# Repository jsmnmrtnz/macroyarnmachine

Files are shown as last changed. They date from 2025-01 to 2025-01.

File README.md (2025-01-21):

Hey!
How exciting you want to build the Macro Yarn Machine. I have built this machine as part of my Master’s project in 2024, and I would have never been able to build it without relying on published Open-Source Hardware projects and the community.

Therefor I want to credit:

1.) Circular Knitic by Varvara Guljajeva and Canet Sola, 2014. https://github.com/var-mar/circular_knitic

2.) HILO Spinning Machine. As I have been working with Sara Diaz Rodriguez closely for the past 2 years and learned about Open-Source Hardware for Textiles from her. https://www.hilotextiles.com/

If you want to credit my machine, please use:
„Macro Yarn Machine“ by Jasmin Martinez, 2024

further information:
Master Thesis: Martinez, Jasmin. Hacking Textile Tools. 2024. Kunsthochschule Weißensee (Weissensee Art Academy).
Mentored by Prof. Christiane Sauer and Prof. Dr. Lucy Norris.

Note: I reverse-documented building the machine, which should explain why the parts are full of soil and grease. Please excuse this and let me know if it makes anything unclear to you. Now – let’s start building!

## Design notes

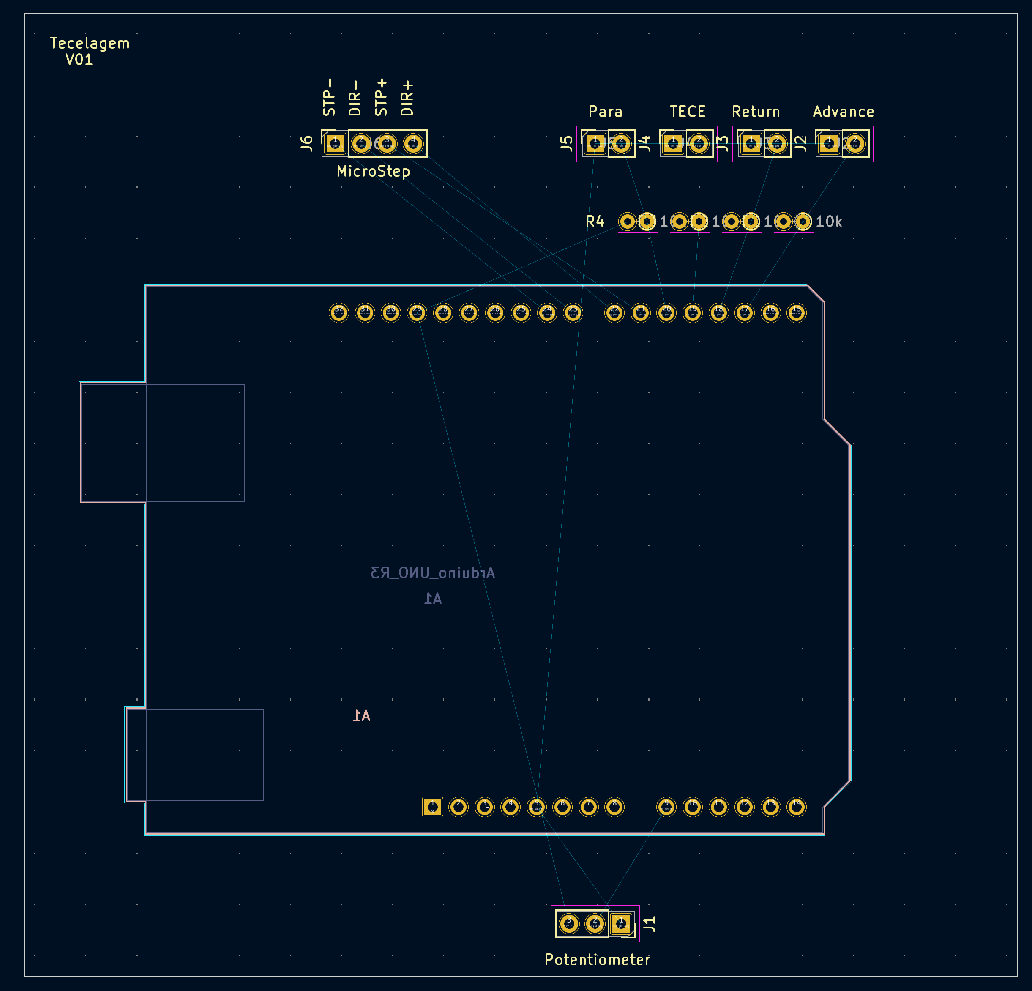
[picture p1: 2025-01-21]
3_Arduino-Electronics/Bildschirmfoto 2024-07-24 um 17.11.13.png

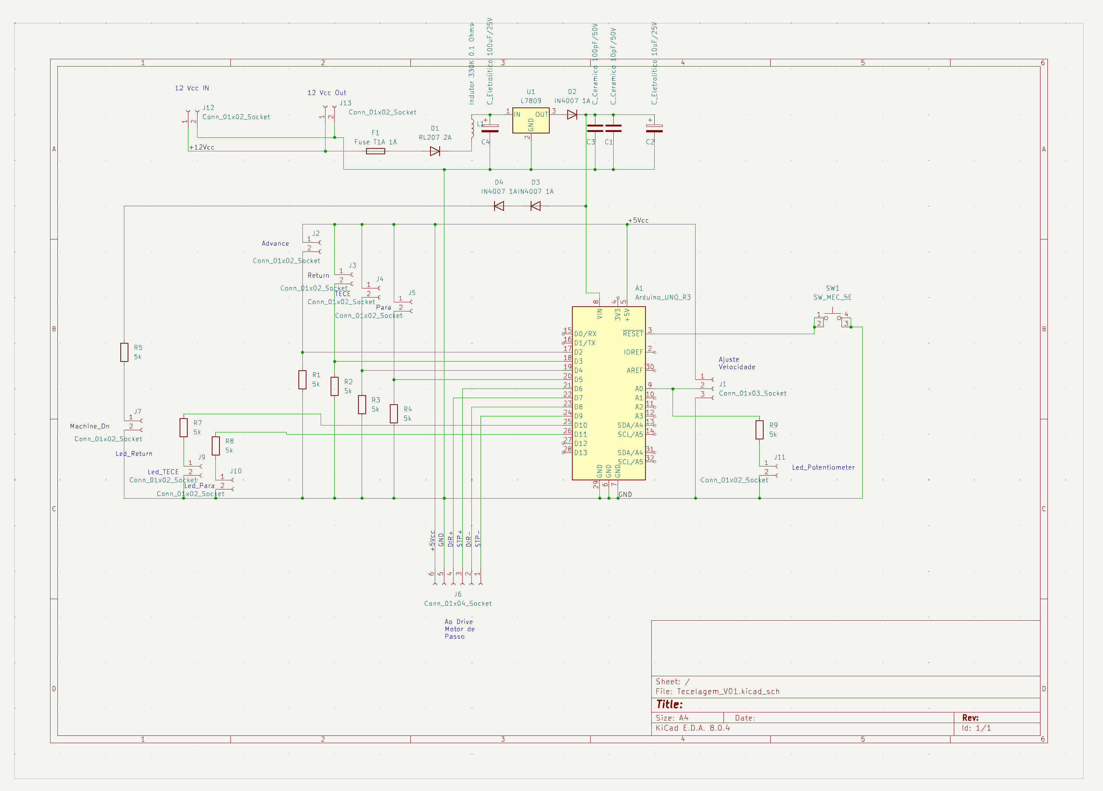
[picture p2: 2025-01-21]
3_Arduino-Electronics/Bildschirmfoto 2024-07-24 um 17.09.53.png

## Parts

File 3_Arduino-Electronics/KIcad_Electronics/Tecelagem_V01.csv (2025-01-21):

# | Reference | Qty | Value | Footprint | DNP
1 | A1 | 1 | Arduino_UNO_R3 | Module:Arduino_UNO_R3
2 | C1 | 1 | C_Ceramico 10pF/50V | Capacitor_THT:C_Disc_D3.0mm_W1.6mm_P2.50mm
3 | C2 | 1 | C_Eletrolitico 10uF/25V | Capacitor_THT:CP_Radial_D5.0mm_P2.50mm
4 | C3 | 1 | C_Ceramico 100pF/50V | Capacitor_THT:C_Disc_D3.0mm_W1.6mm_P2.50mm
5 | C4 | 1 | C_Eletrolitico 100uF/25V | Capacitor_THT:CP_Radial_D5.0mm_P2.50mm
6 | D1 | 1 | RL207 2A | Diode_THT:D_DO-27_P5.08mm_Vertical_AnodeUp
7 | D2, D3, D4 | 3 | IN4007 1A | Diode_THT:D_DO-15_P3.81mm_Vertical_AnodeUp
8 | F1 | 1 | Fuse T1A 1A | Fuse:Fuse_Littelfuse_372_D8.50mm
9 | J1 | 1 | Conn_01x03_Socket | Connector_Molex:Molex_KK-254_AE-6410-03A_1x03_P2.54mm_Vertical
10 | J2, J3, J4, J5, J7, J9, J10, J11 | 8 | Conn_01x02_Socket | Connector_Molex:Molex_KK-254_AE-6410-02A_1x02_P2.54mm_Vertical
11 | J6 | 1 | Conn_01x04_Socket | Connector_Molex:Molex_KK-254_AE-6410-06A_1x06_P2.54mm_Vertical
12 | J12, J13 | 2 | Conn_01x02_Socket | Connector_Molex:Molex_KK-396_A-41791-0002_1x02_P3.96mm_Vertical
13 | L1 | 1 | Indutor 330K 0,1 Ohms | Inductor_THT:L_Radial_D7.8mm_P5.00mm_Fastron_07HCP
14 | R1, R2, R3, R4, R5, R7, R8, R9 | 8 | 5k | Resistor_THT:R_Axial_DIN0204_L3.6mm_D1.6mm_P1.90mm_Vertical
15 | SW1 | 1 | SW_MEC_5E | Chave_Tactil:Tactil_6mm
16 | U1 | 1 | L7809 | Package_TO_SOT_THT:TO-126-3_Vertical

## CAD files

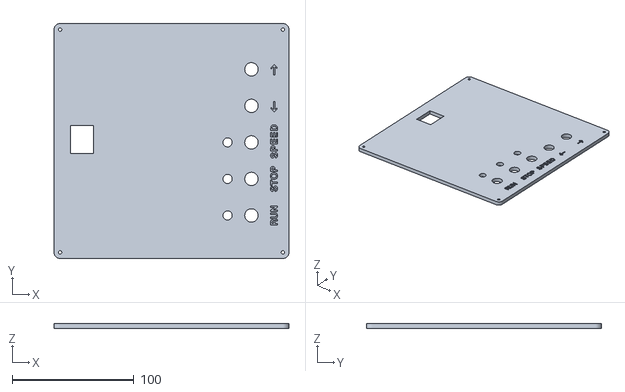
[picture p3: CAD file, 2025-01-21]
2_STLs/Electronic Board/Electronics-Control-Board.stl
193.0 x 193.0 x 4.00

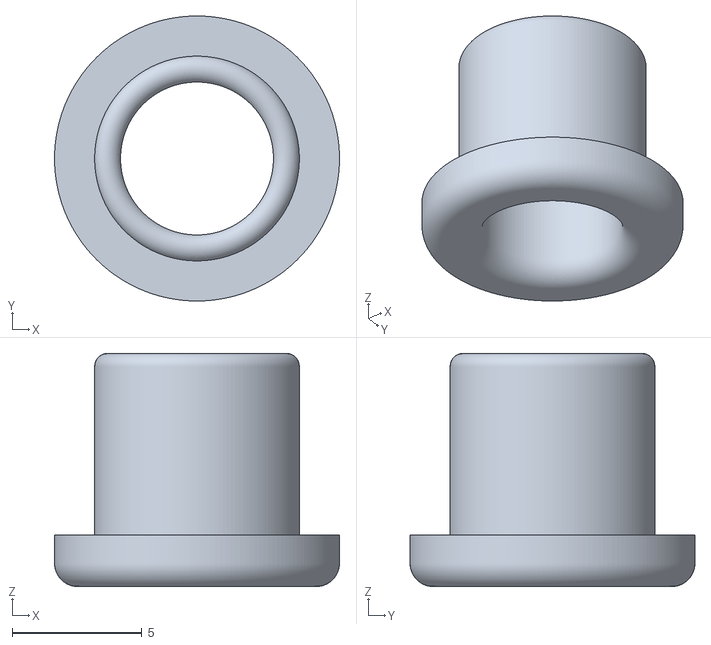
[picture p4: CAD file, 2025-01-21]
2_STLs/Eyelet.stl
11.0 x 11.0 x 9.00

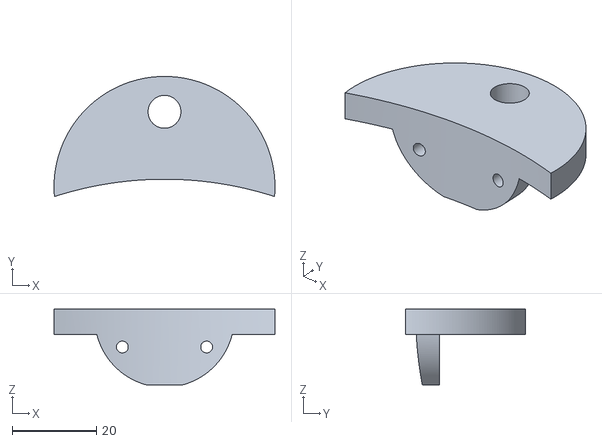
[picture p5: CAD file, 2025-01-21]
2_STLs/Machine Body/4xHolder-for-threaded-rods.stl
52.4 x 28.5 x 18.0

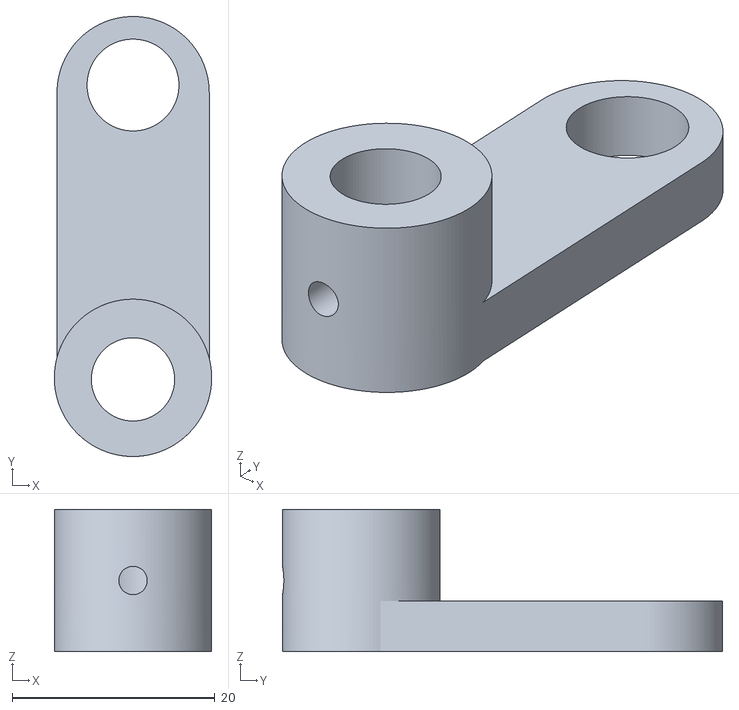
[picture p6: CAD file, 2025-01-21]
2_STLs/Yarn Guidance/4x-yarn-wing-guide.stl
15.5 x 43.3 x 14.0

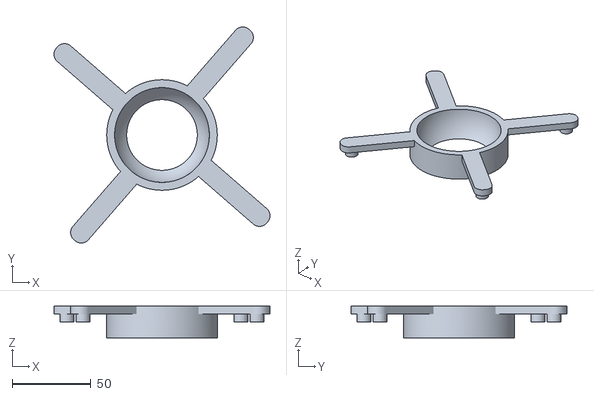
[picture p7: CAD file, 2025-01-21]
2_STLs/funnel.stl
136.8 x 136.8 x 20.0

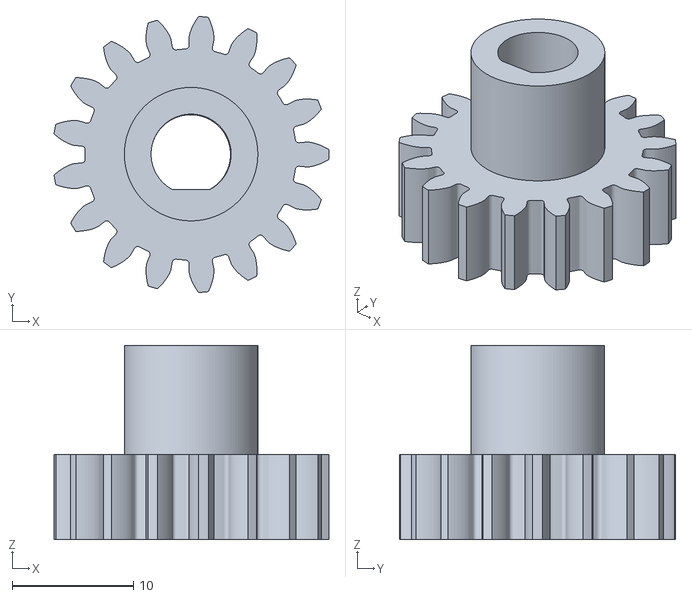
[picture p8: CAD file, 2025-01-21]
2_STLs/Machine Body/small-motor-gear2.stl
22.7 x 22.8 x 16.0

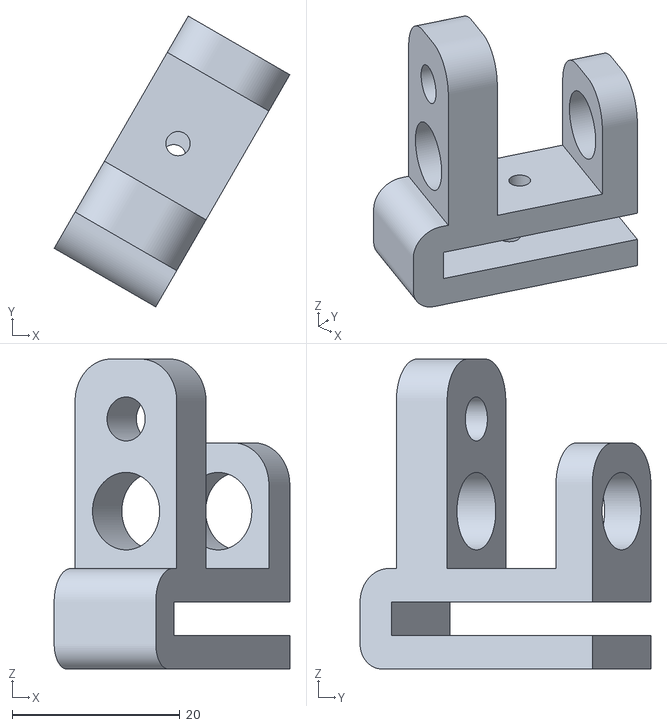
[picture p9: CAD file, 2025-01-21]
2_STLs/Yarn Guidance/4x-yarn-tension-holder.stl
28.1 x 34.7 x 37.0

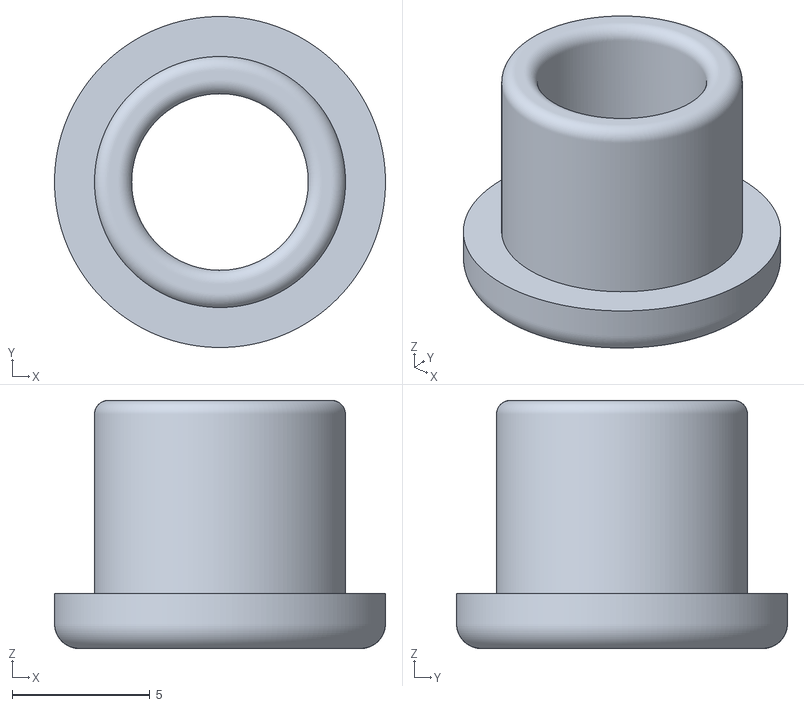
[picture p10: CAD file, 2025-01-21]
2_STLs/eyelet-final.stl
12.0 x 12.0 x 9.00

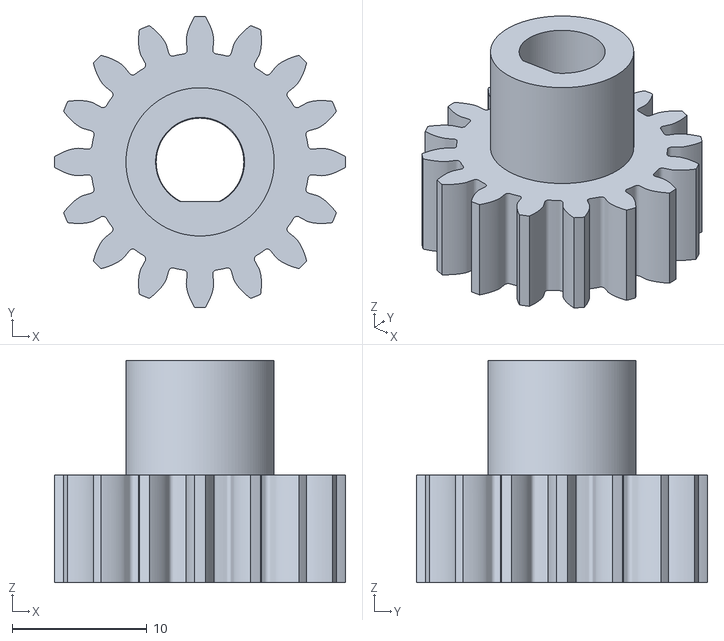
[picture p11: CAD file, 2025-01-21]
2_STLs/Machine Body/small-motor-gear-1.stl
21.6 x 21.6 x 16.5

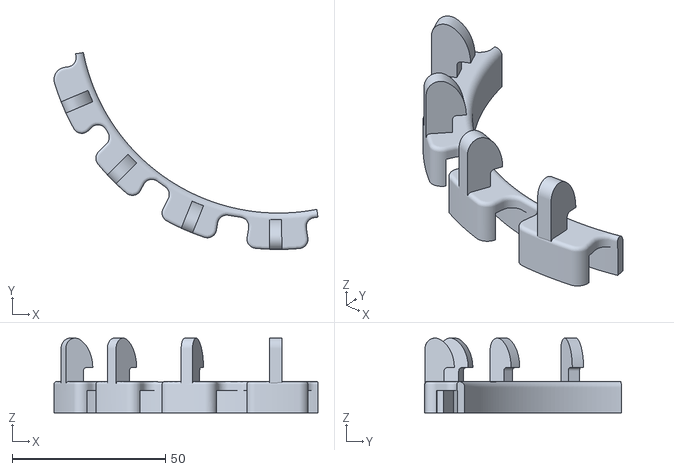
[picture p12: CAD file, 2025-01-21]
2_STLs/Yarn Guidance/Needle-Holder.stl
86.1 x 64.2 x 24.4

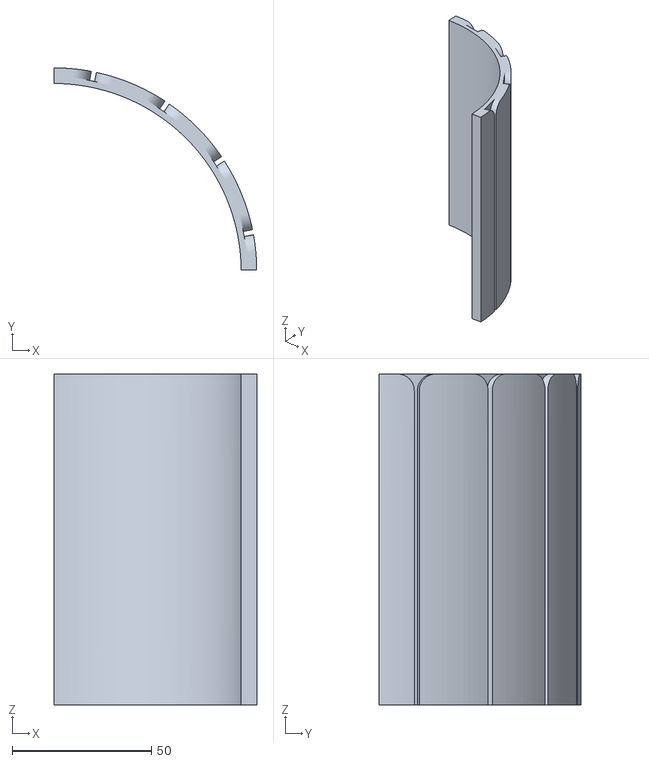
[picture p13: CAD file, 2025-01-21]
2_STLs/Machine Body/4x-inner-cylinder.stl
72.8 x 72.7 x 119.0

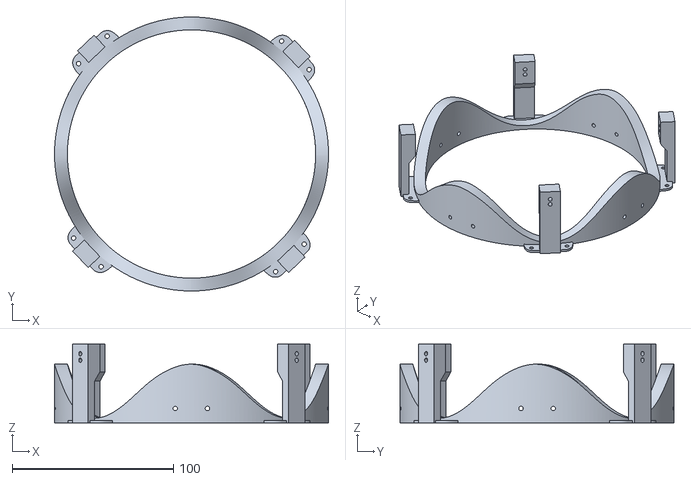
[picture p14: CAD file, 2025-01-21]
2_STLs/Machine Body/needle-guide-bottom.stl
170.0 x 170.0 x 49.0

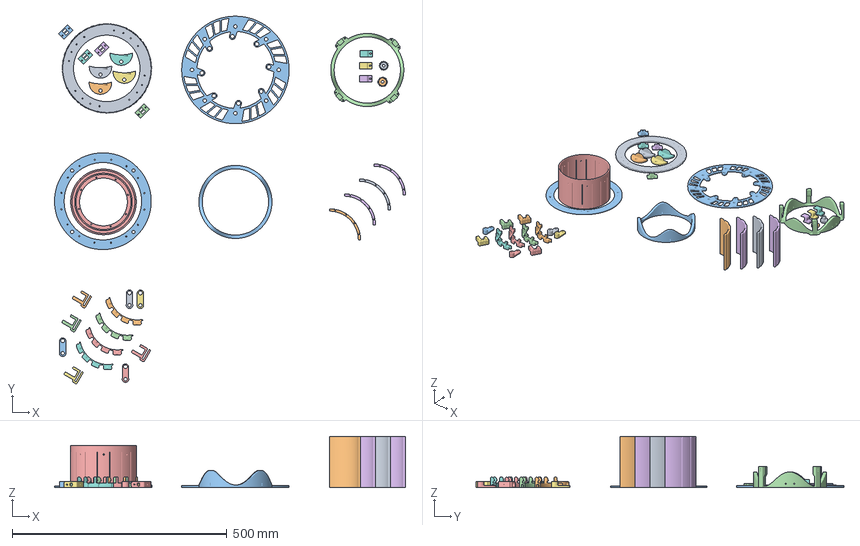
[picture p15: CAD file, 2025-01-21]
2_STLs/Machine Body/4xBearings.3mf
816.6 x 855.3 x 119.0 mm
Big Bottom Gear.stl
Needle-Holder.stl x 4
needle-guide-top.stl
4x-inner-cylinder.stl x 4
4xHolder-for-threaded-rods.stl x 4
4x-yarn-tension-holder.stl x 4
4xBearings.stl x 4
4x-yarn-wing-guide.stl x 4
Middle-Layer.stl
needle-guide-bottom.stl
Outer-Cylinder-Final.stl
Bottom-Gear-Fix.stl x 3
small-motor-gear-1.stl
small-motor-gear2.stl
Top-Layer.stl

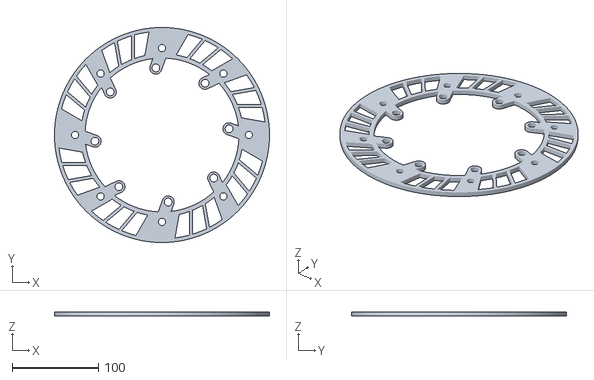
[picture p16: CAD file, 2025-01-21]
2_STLs/Machine Body/Middle-Layer.stl
250.0 x 250.0 x 5.00

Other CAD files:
2_STLs/Machine Body/needle-guide-top.stl
2_STLs/Machine Body/Bottom-Gear-Fix.stl
2_STLs/Machine Body/Outer-Cylinder-Final.stl
2_STLs/Machine Body/Top-Layer.stl
2_STLs/Machine Body/4xBearings.stl
2_STLs/Machine Body/Big Bottom Gear.stl

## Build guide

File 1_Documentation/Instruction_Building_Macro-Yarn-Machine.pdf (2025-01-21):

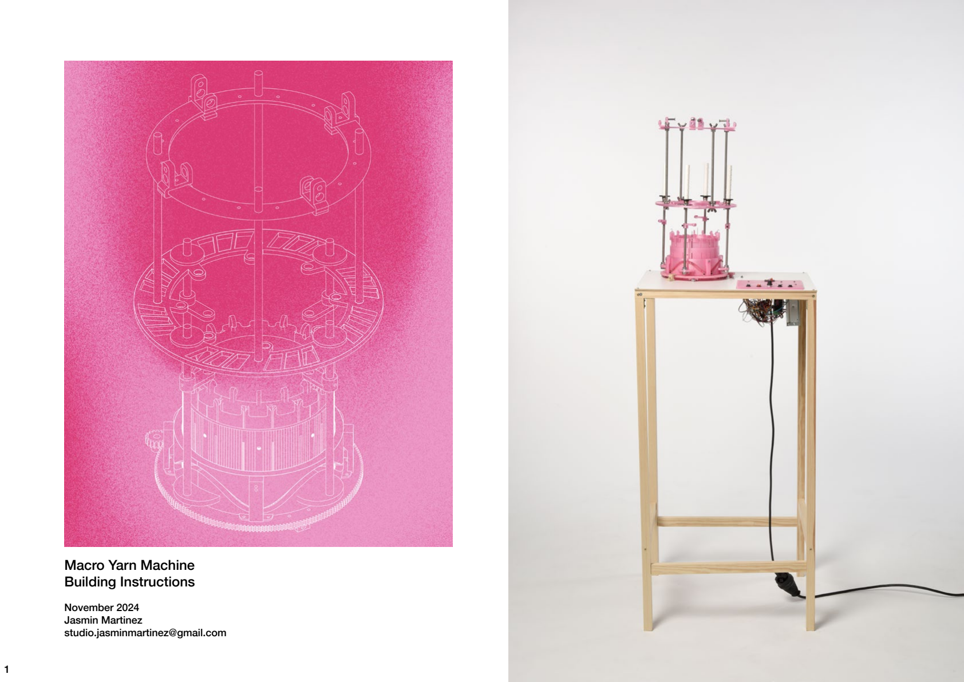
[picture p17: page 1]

Macro Yarn Machine
Building Instructions

November 2024
Jasmin Martinez
studio.jasminmartinez@gmail.com

Hey!
How exciting you want to build the Macro Yarn Machine. I have built this machine as part of my Master’s project in 2024, and I would have never been able to build it without relying on published Open-Source Hardware projects and the community.
Therefor I want to credit:
1.) Circular Knitic by Varvara Guljajeva and Canet Sola, 2014. https://github.com/var-mar/circular_knitic
2.) HILO Spinning Machine. As I have been working with Sara Diaz Rodriguez closely for the past 2 years and learned about Open Textile Hardware from her. https://www.hilotextiles.com/
If you want to credit my machine, please use:
„Macro Yarn Machine“ by Jasmin Martinez, 2024
further information:
Master Thesis: Martinez, Jasmin. Hacking Textile Tools. 2024. Kunsthochschule Weißensee (Weissensee Art Academy). Mentored by Prof. Christiane Sauer and Prof. Dr. Lucy Norris. Note: I reverse-documented building the machine, which should explain why the parts are full of soil and grease. Please excuse this and let me know if it makes anything un-clear to you.
Now – let’s start building!

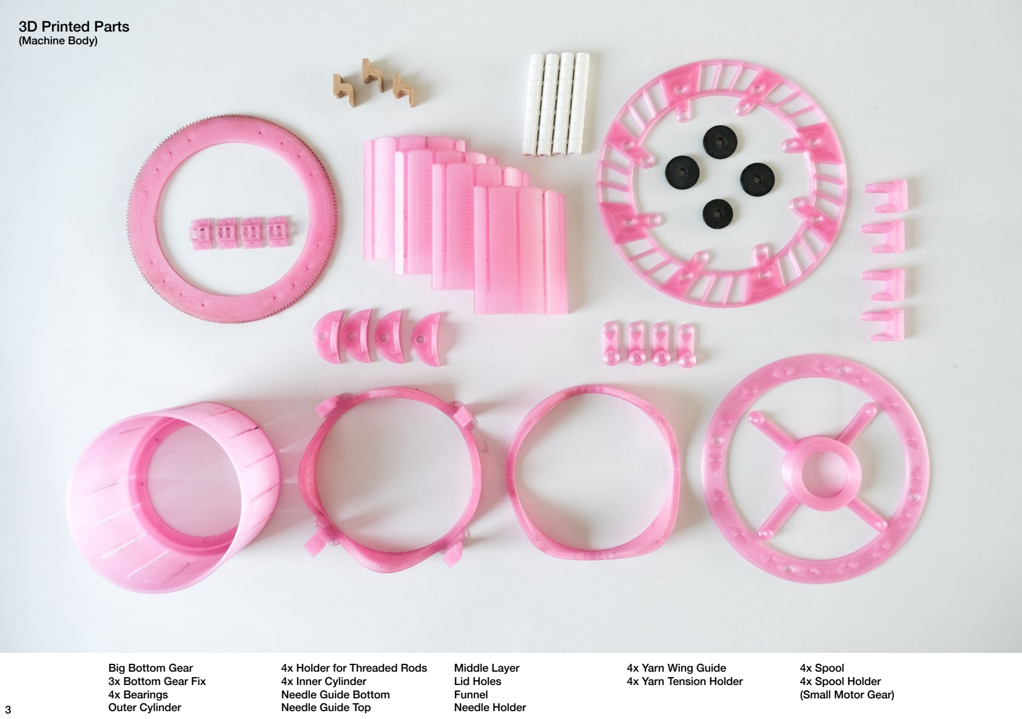
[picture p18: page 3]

3D Printed Parts
(Machine Body)

Big Bottom Gear
3x Bottom Gear Fix
4x Bearings
Outer Cylinder

4x Holder for Threaded Rods 4x Inner Cylinder
Needle Guide Bottom
Needle Guide Top

Middle Layer
Lid Holes
Funnel
Needle Holder

4x Yarn Wing Guide
4x Yarn Tension Holder

4x Spool
4x Spool Holder
(Small Motor Gear)

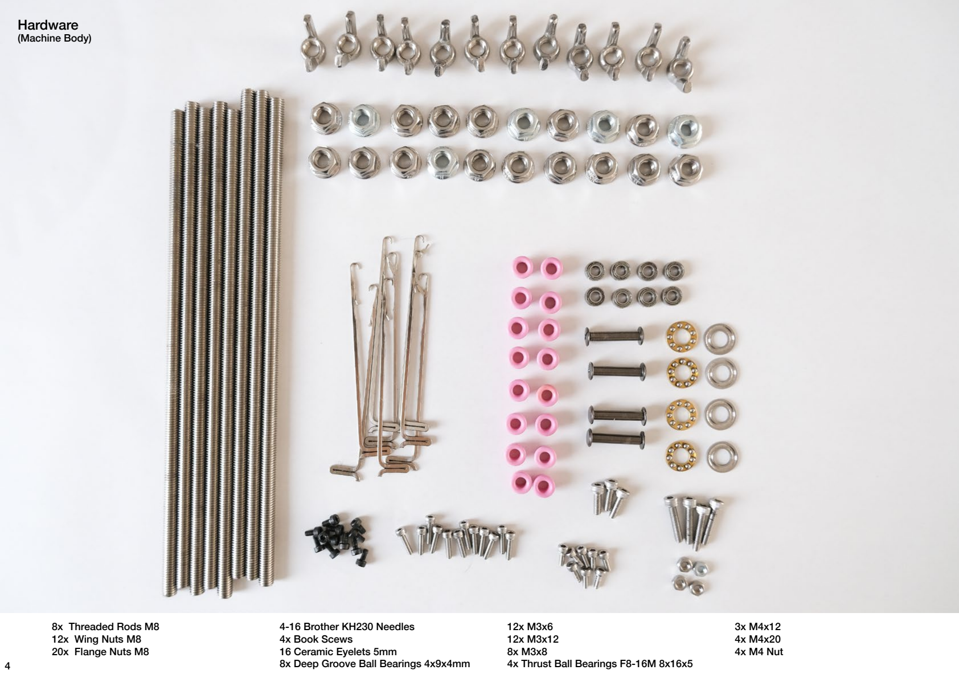
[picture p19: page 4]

Hardware
(Machine Body)

8x Threaded Rods M8
12x Wing Nuts M8
20x Flange Nuts M8

4-16 Brother KH230 Needles
4x Book Scews
16 Ceramic Eyelets 5mm
8x Deep Groove Ball Bearings 4x9x4mm

12x M3x6
12x M3x12
8x M3x8
4x Thrust Ball Bearings F8-16M 8x16x5

3x M4x12
4x M4x20
4x M4 Nut

Bottom Gear

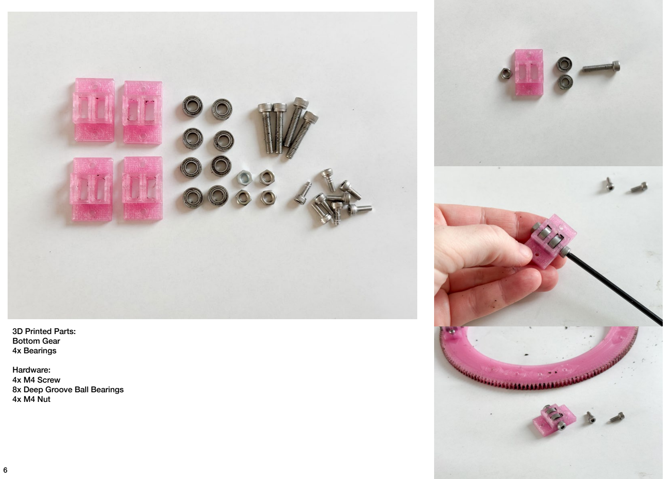
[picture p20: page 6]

3D Printed Parts:
Bottom Gear
4x Bearings
Hardware:
4x M4 Screw
8x Deep Groove Ball Bearings 4x M4 Nut

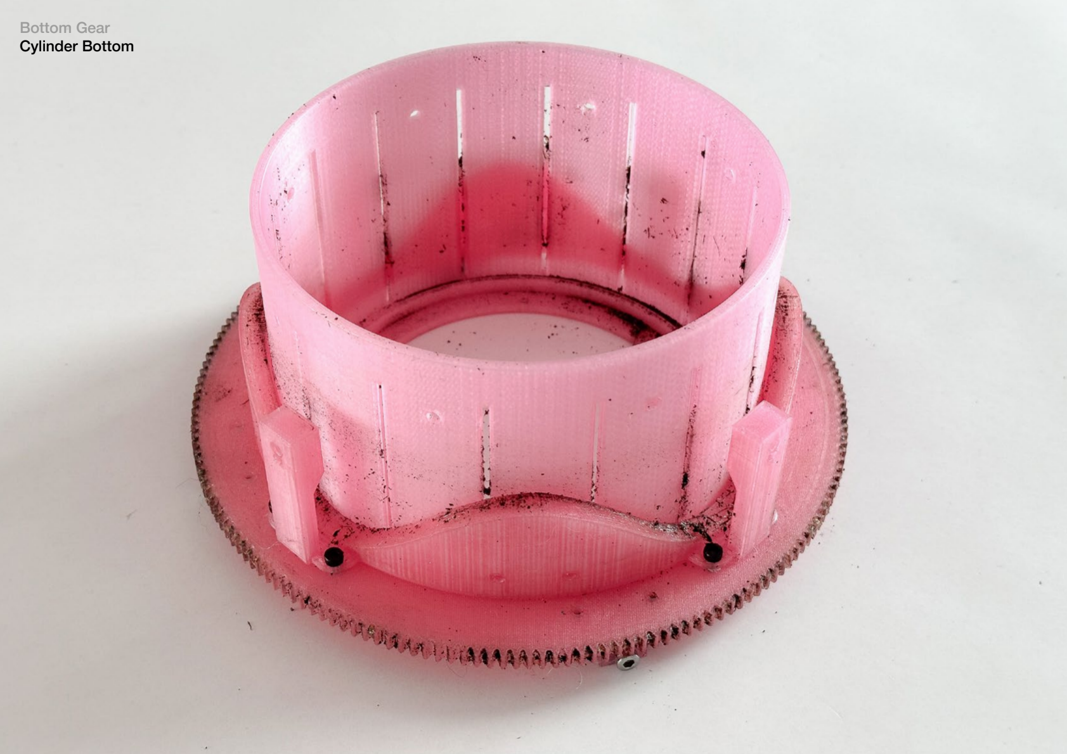
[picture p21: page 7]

Bottom Gear
Cylinder Bottom

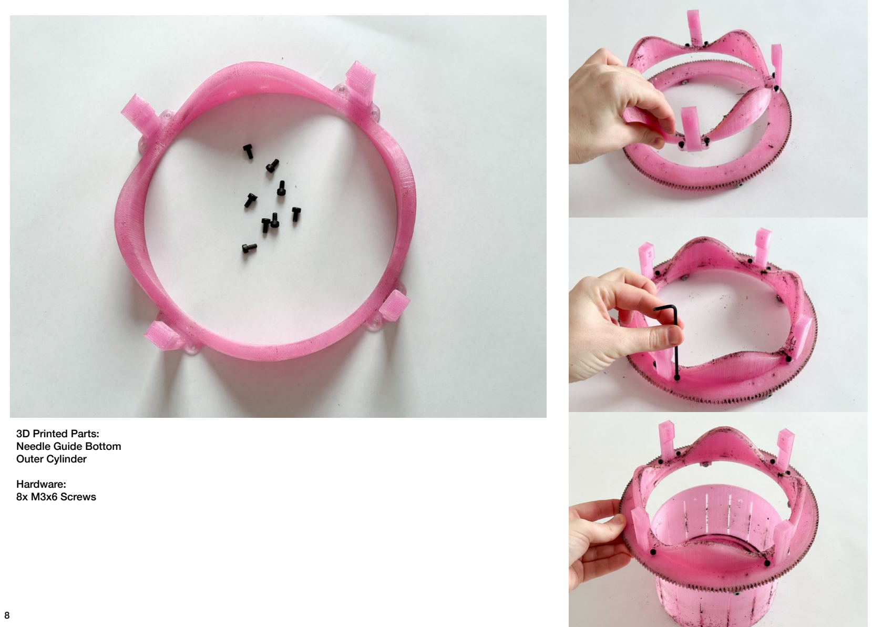
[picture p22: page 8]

3D Printed Parts:
Needle Guide Bottom
Outer Cylinder
Hardware:
8x M3x6 Screws

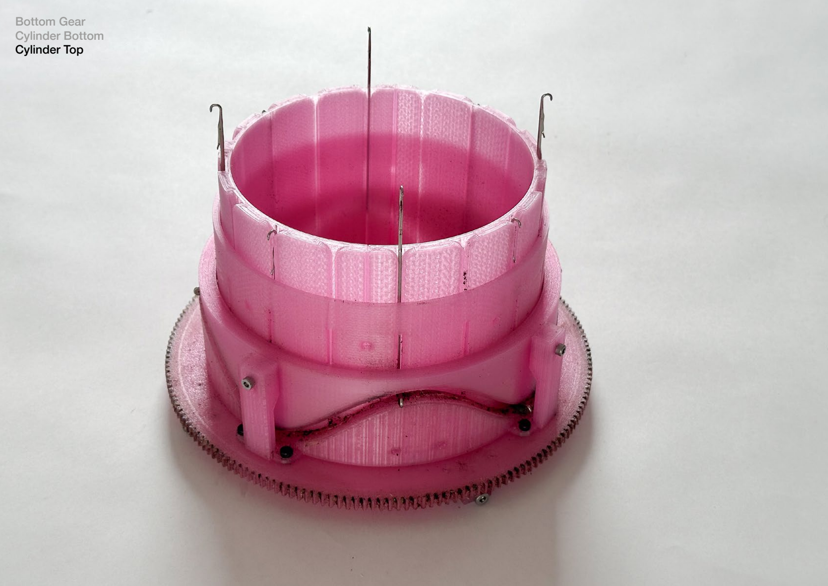
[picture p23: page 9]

Bottom Gear
Cylinder Bottom
Cylinder Top

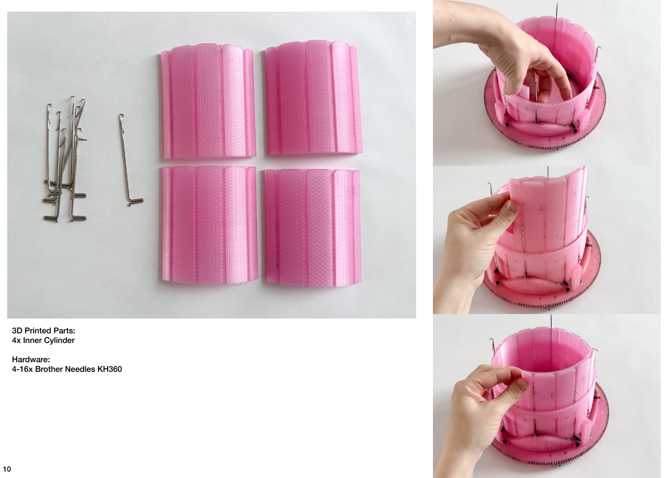
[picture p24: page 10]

3D Printed Parts:
4x Inner Cylinder
Hardware:
4-16x Brother Needles KH360

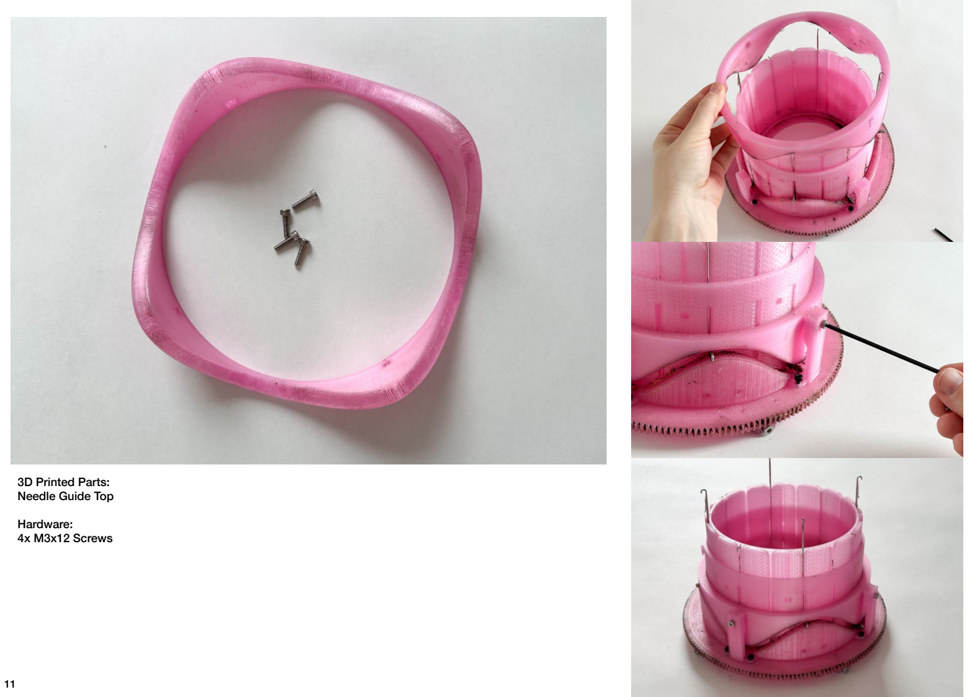
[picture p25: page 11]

3D Printed Parts:
Needle Guide Top
Hardware:
4x M3x12 Screws

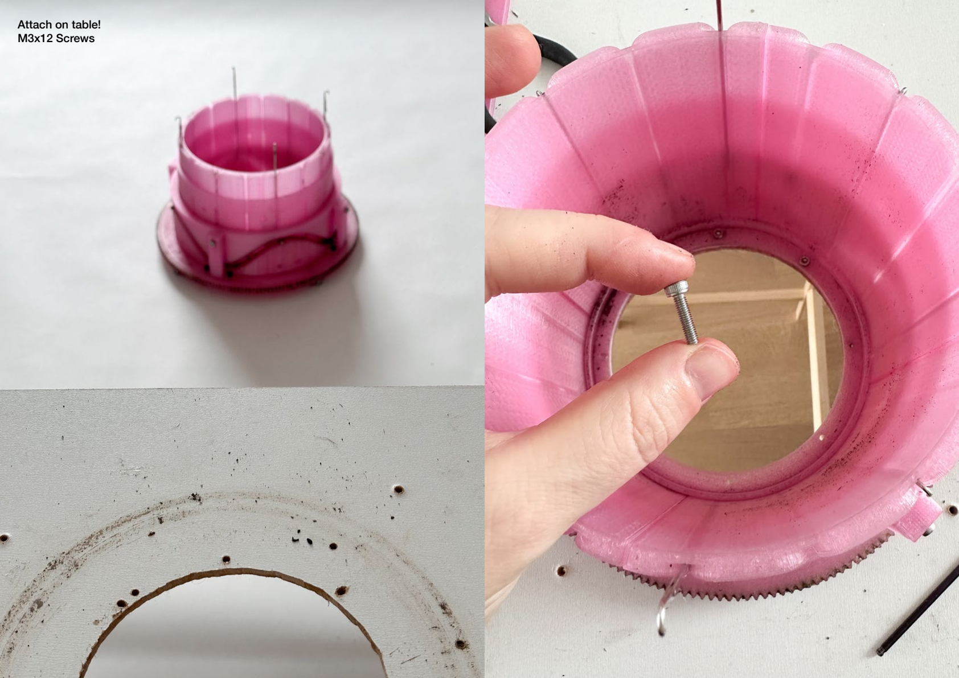
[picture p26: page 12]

Attach on table!
M3x12 Screws

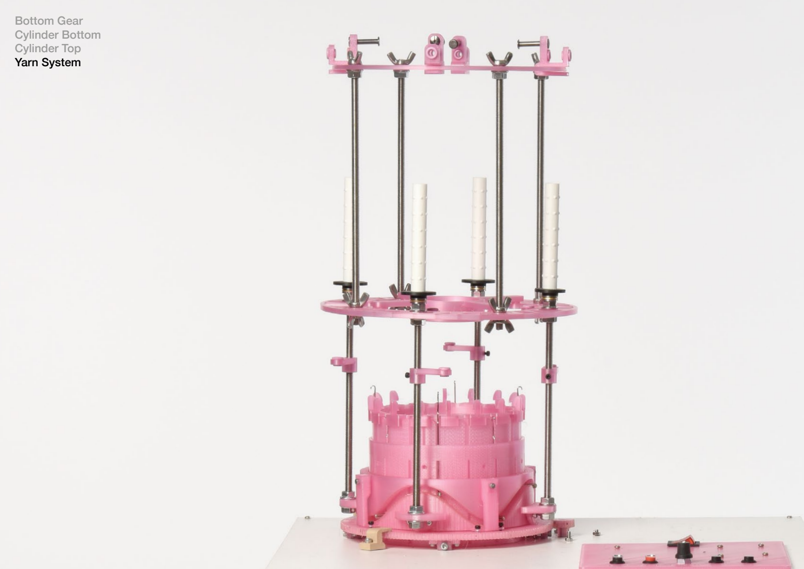
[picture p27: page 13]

Bottom Gear
Cylinder Bottom
Cylinder Top
Yarn System

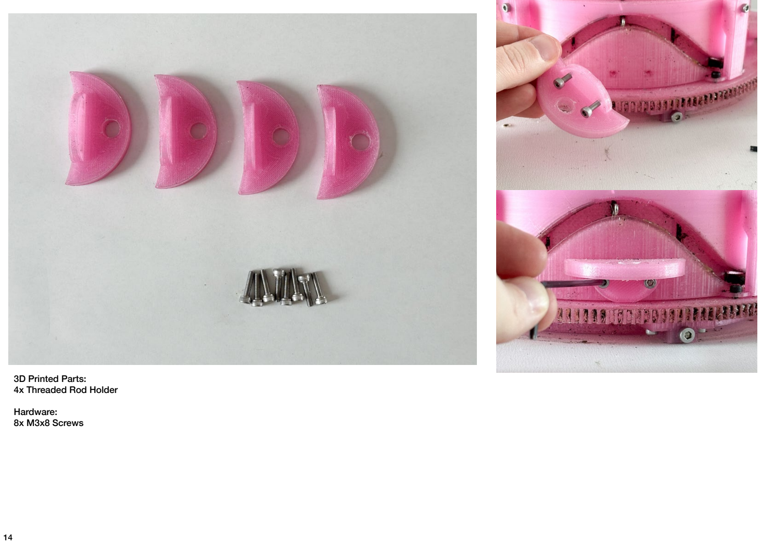
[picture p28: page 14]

3D Printed Parts:
4x Threaded Rod Holder
Hardware:
8x M3x8 Screws

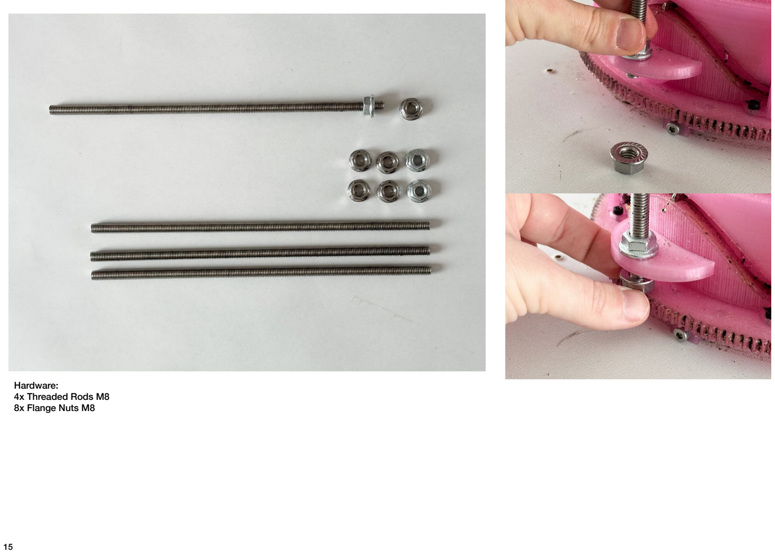
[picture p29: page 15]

Hardware:
4x Threaded Rods M8
8x Flange Nuts M8

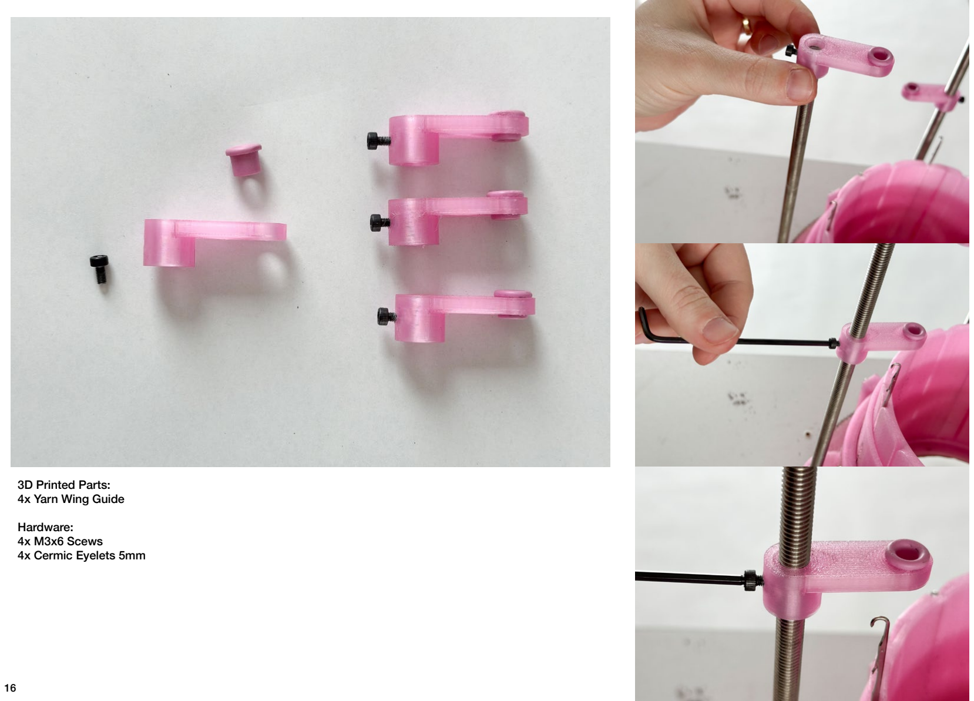
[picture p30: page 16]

3D Printed Parts:
4x Yarn Wing Guide
Hardware:
4x M3x6 Scews
4x Cermic Eyelets 5mm

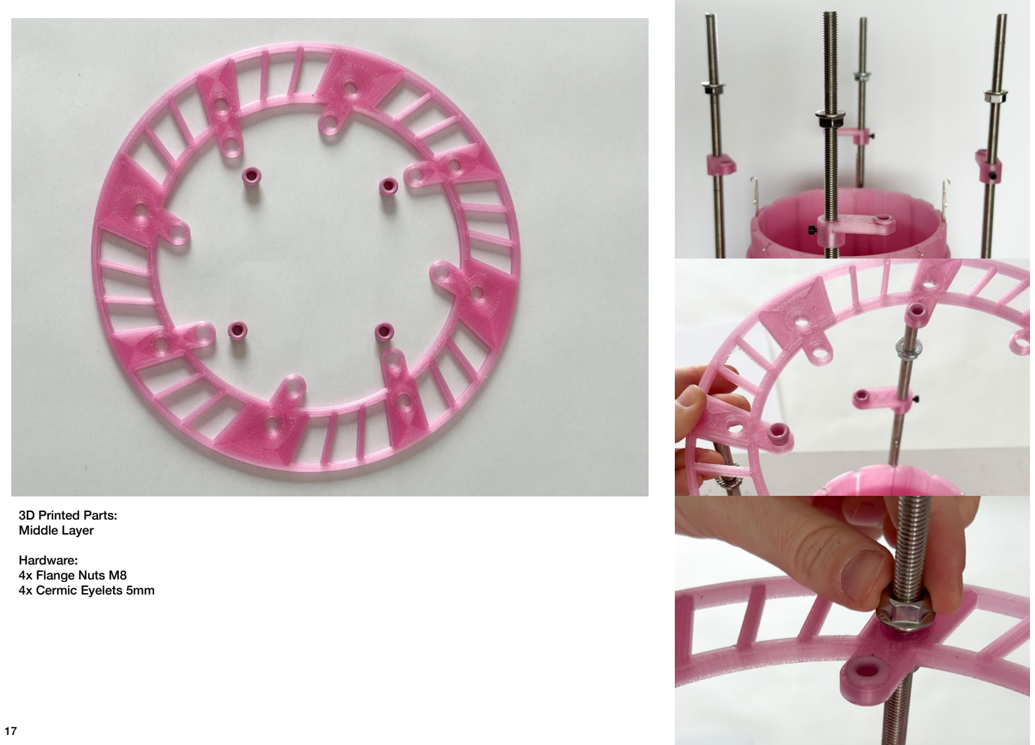
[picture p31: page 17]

3D Printed Parts:
Middle Layer
Hardware:
4x Flange Nuts M8
4x Cermic Eyelets 5mm

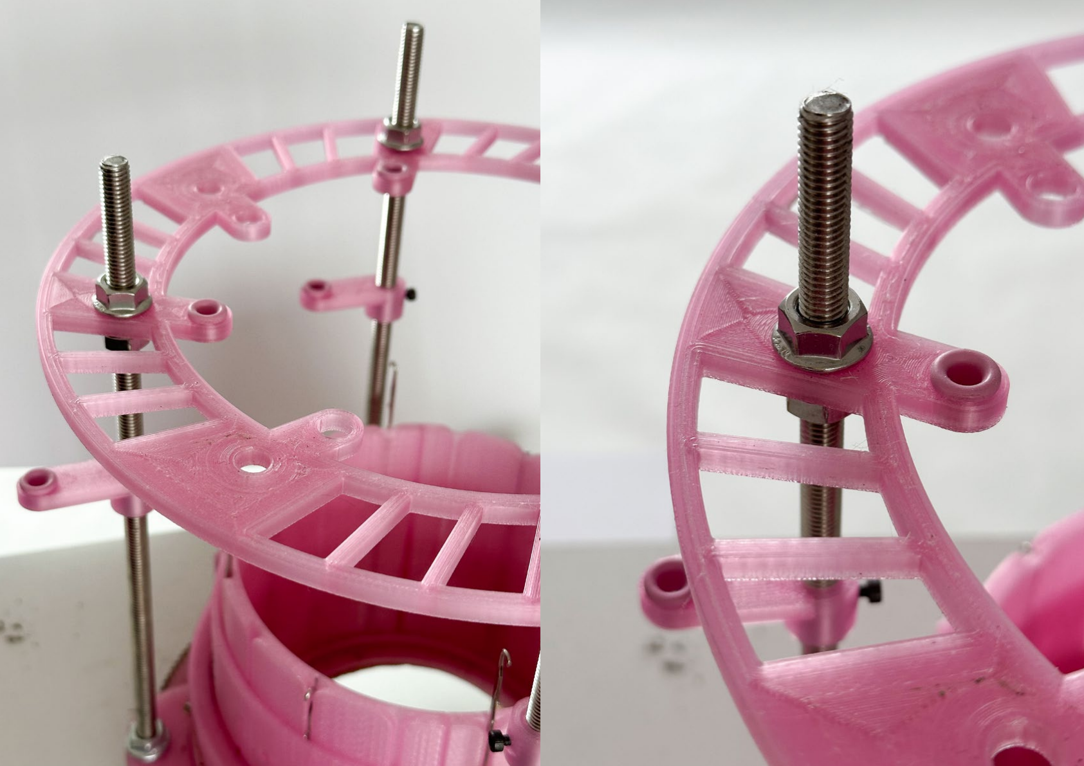
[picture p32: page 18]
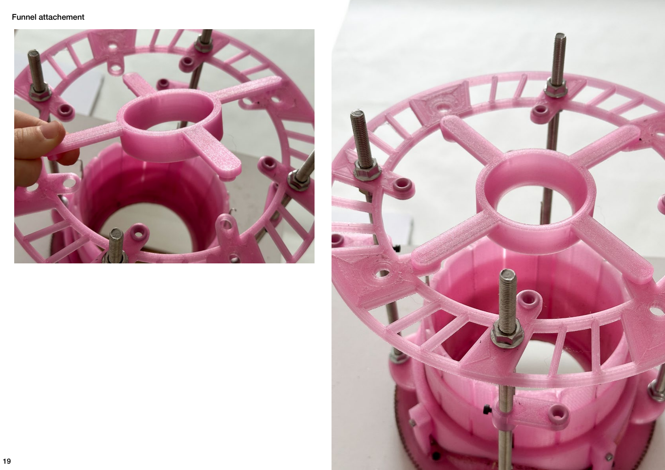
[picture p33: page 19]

Funnel attachement

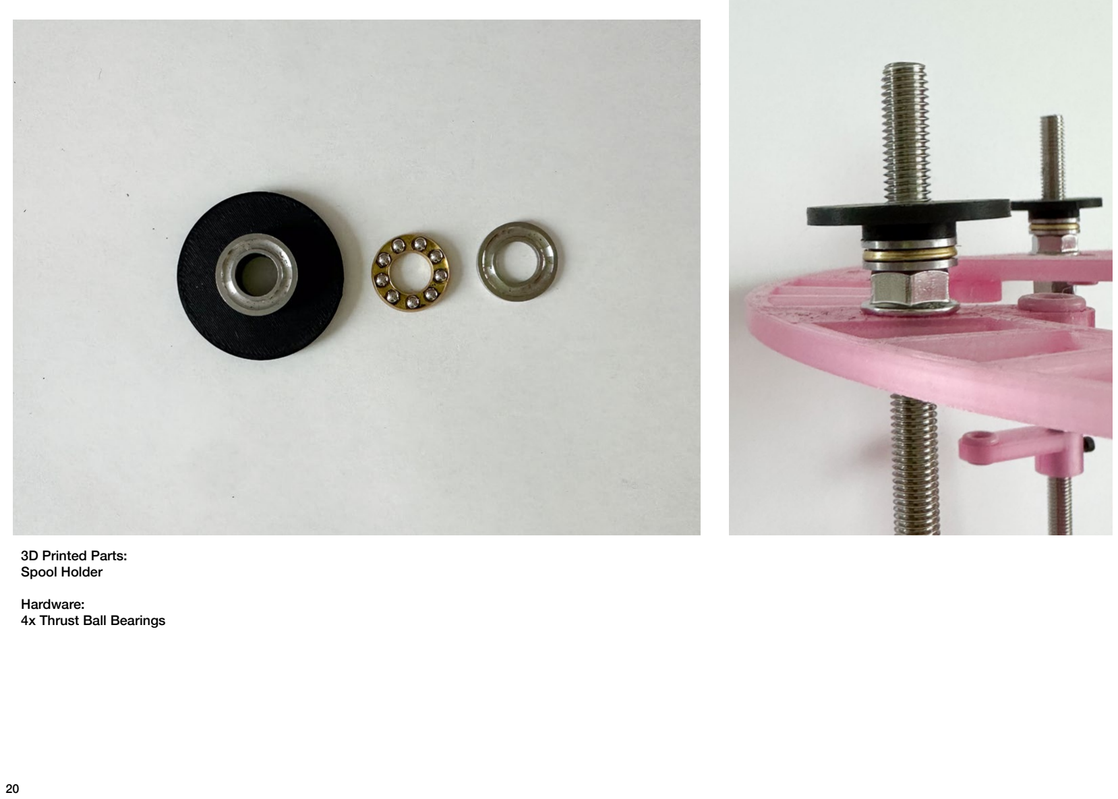
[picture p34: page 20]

3D Printed Parts:
Spool Holder
Hardware:
4x Thrust Ball Bearings

Hardware:
8x Wing Nuts M8
4x Threaded Rods M8

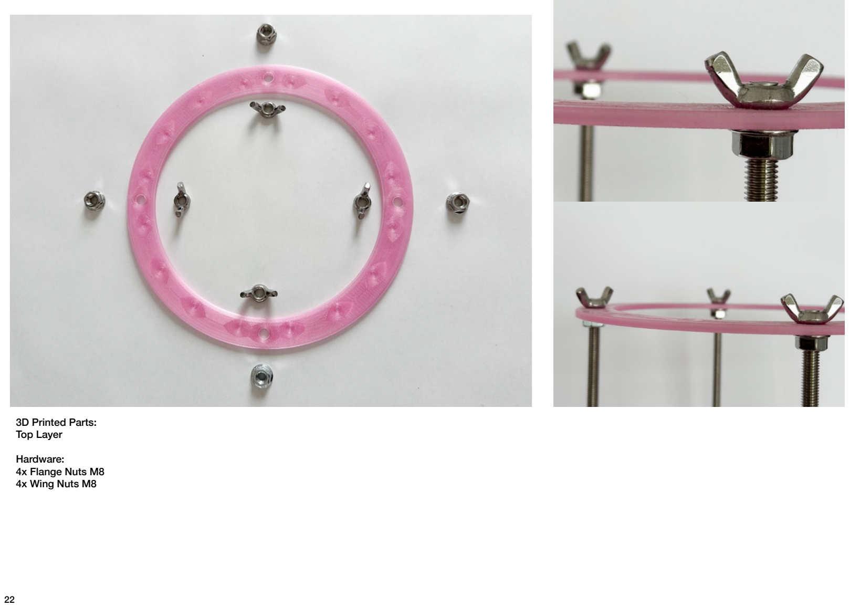
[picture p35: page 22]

3D Printed Parts:
Top Layer
Hardware:
4x Flange Nuts M8
4x Wing Nuts M8

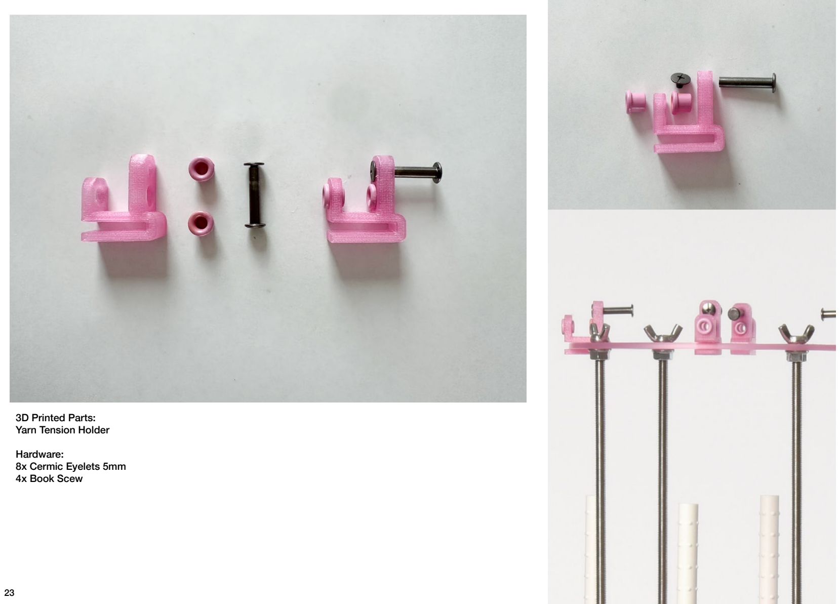
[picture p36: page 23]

3D Printed Parts:
Yarn Tension Holder
Hardware:
8x Cermic Eyelets 5mm
4x Book Scew

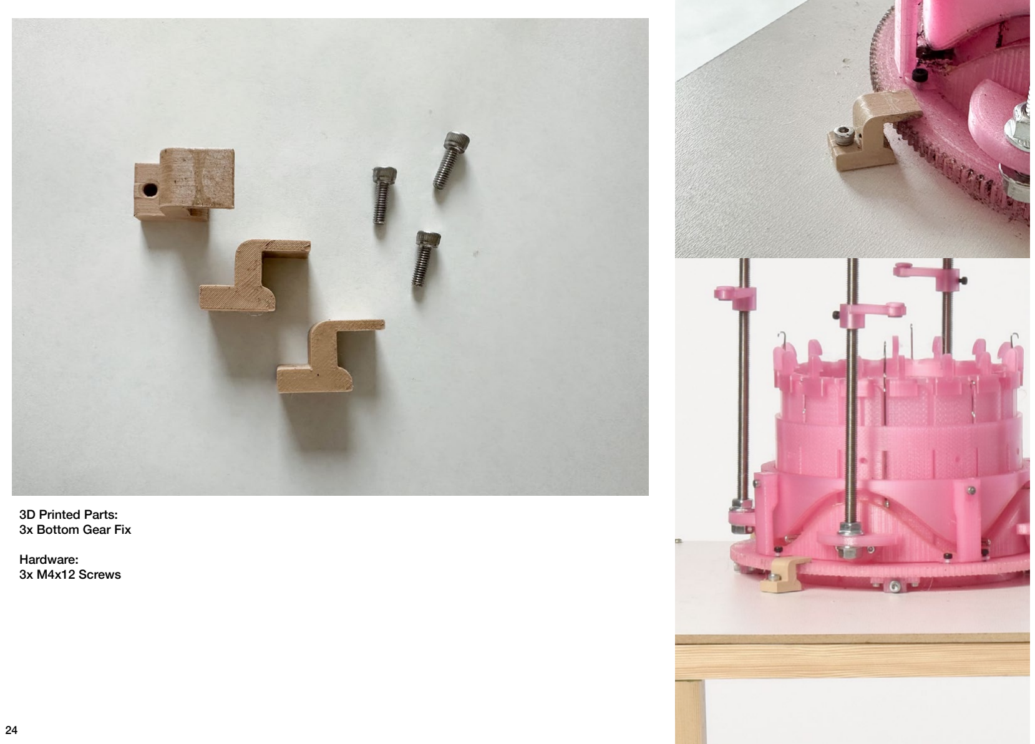
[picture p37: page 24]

3D Printed Parts:
3x Bottom Gear Fix
Hardware:
3x M4x12 Screws

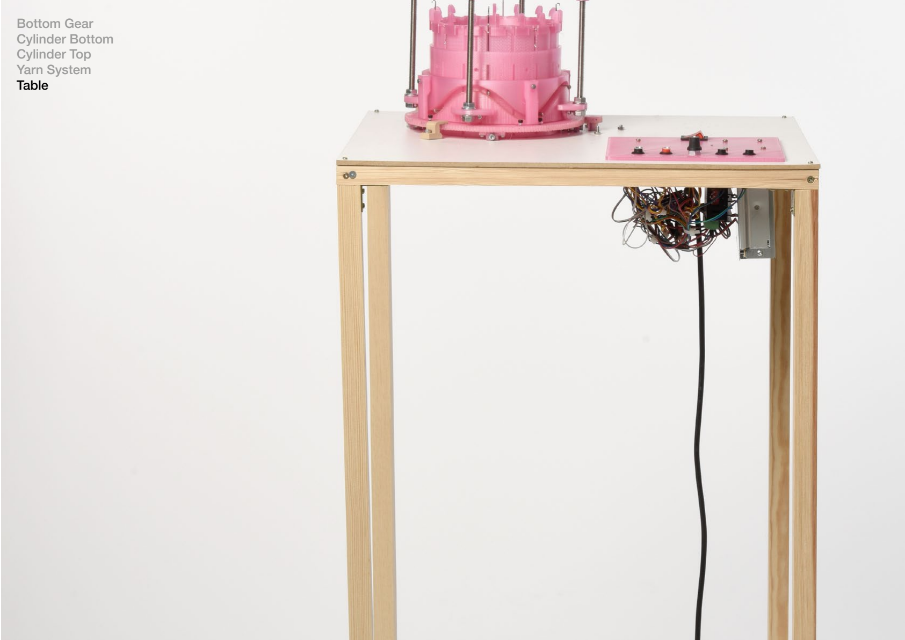
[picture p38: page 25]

Bottom Gear
Cylinder Bottom
Cylinder Top
Yarn System
Table

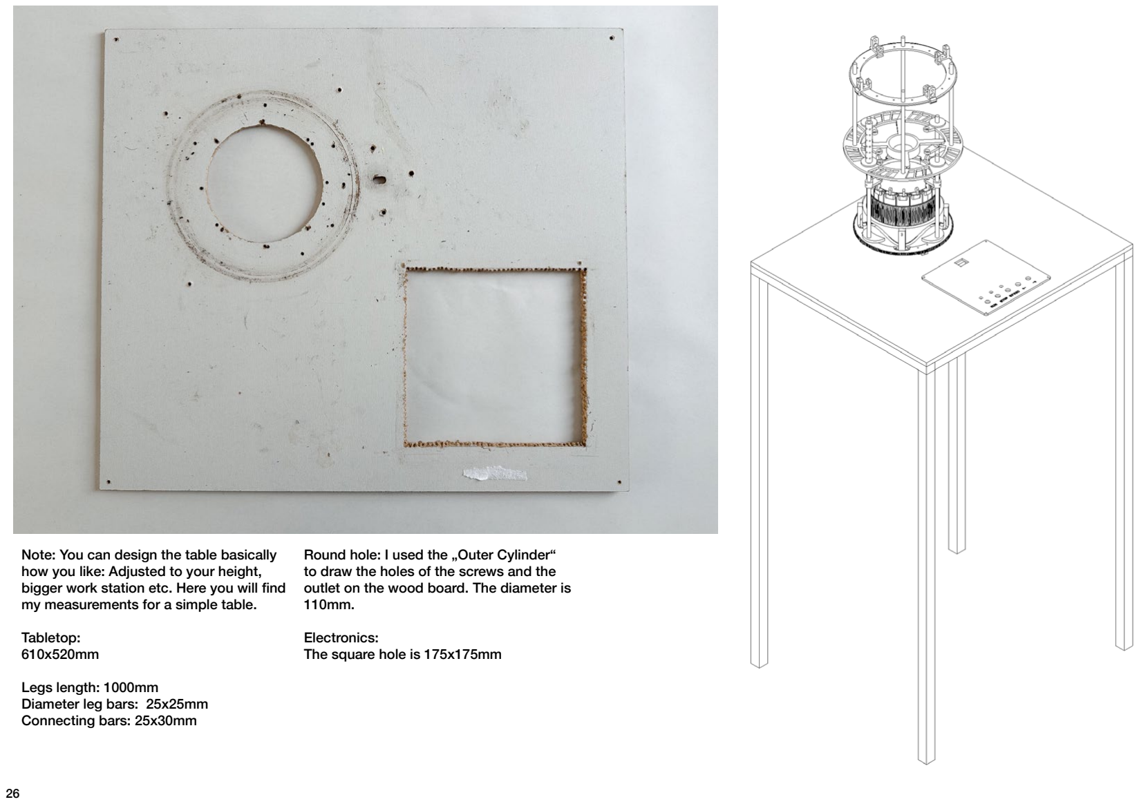
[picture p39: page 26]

Note: You can design the table basically how you like: Adjusted to your height, bigger work station etc. Here you will find my measurements for a simple table. Tabletop:
610x520mm
Legs length: 1000mm
Diameter leg bars: 25x25mm Connecting bars: 25x30mm

Round hole: I used the „Outer Cylinder“ to draw the holes of the screws and the outlet on the wood board. The diameter is 110mm.
Electronics:
The square hole is 175x175mm

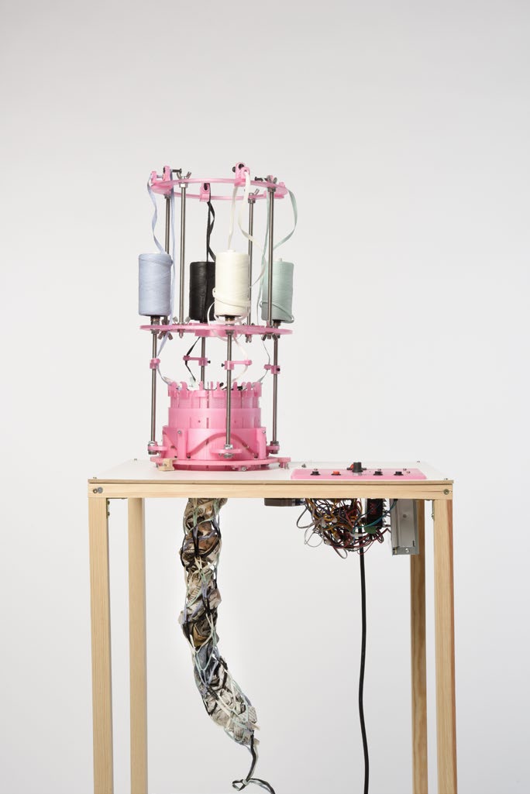
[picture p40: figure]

End Notes:
You will find a STL File named „Needle Holder“ – you can also print those but I had the feeling it doesn’t quite work the way it should. Any feedback is welcome!
Anyway: You build your Macro Yarn Machine
– congratulations!
I’m happy to collaborate for further developments, contact me via E-Mail: studio.jasminmartinez@gmail.com
Let me and others find your process and developments via the hashtag #macroyarnmachine

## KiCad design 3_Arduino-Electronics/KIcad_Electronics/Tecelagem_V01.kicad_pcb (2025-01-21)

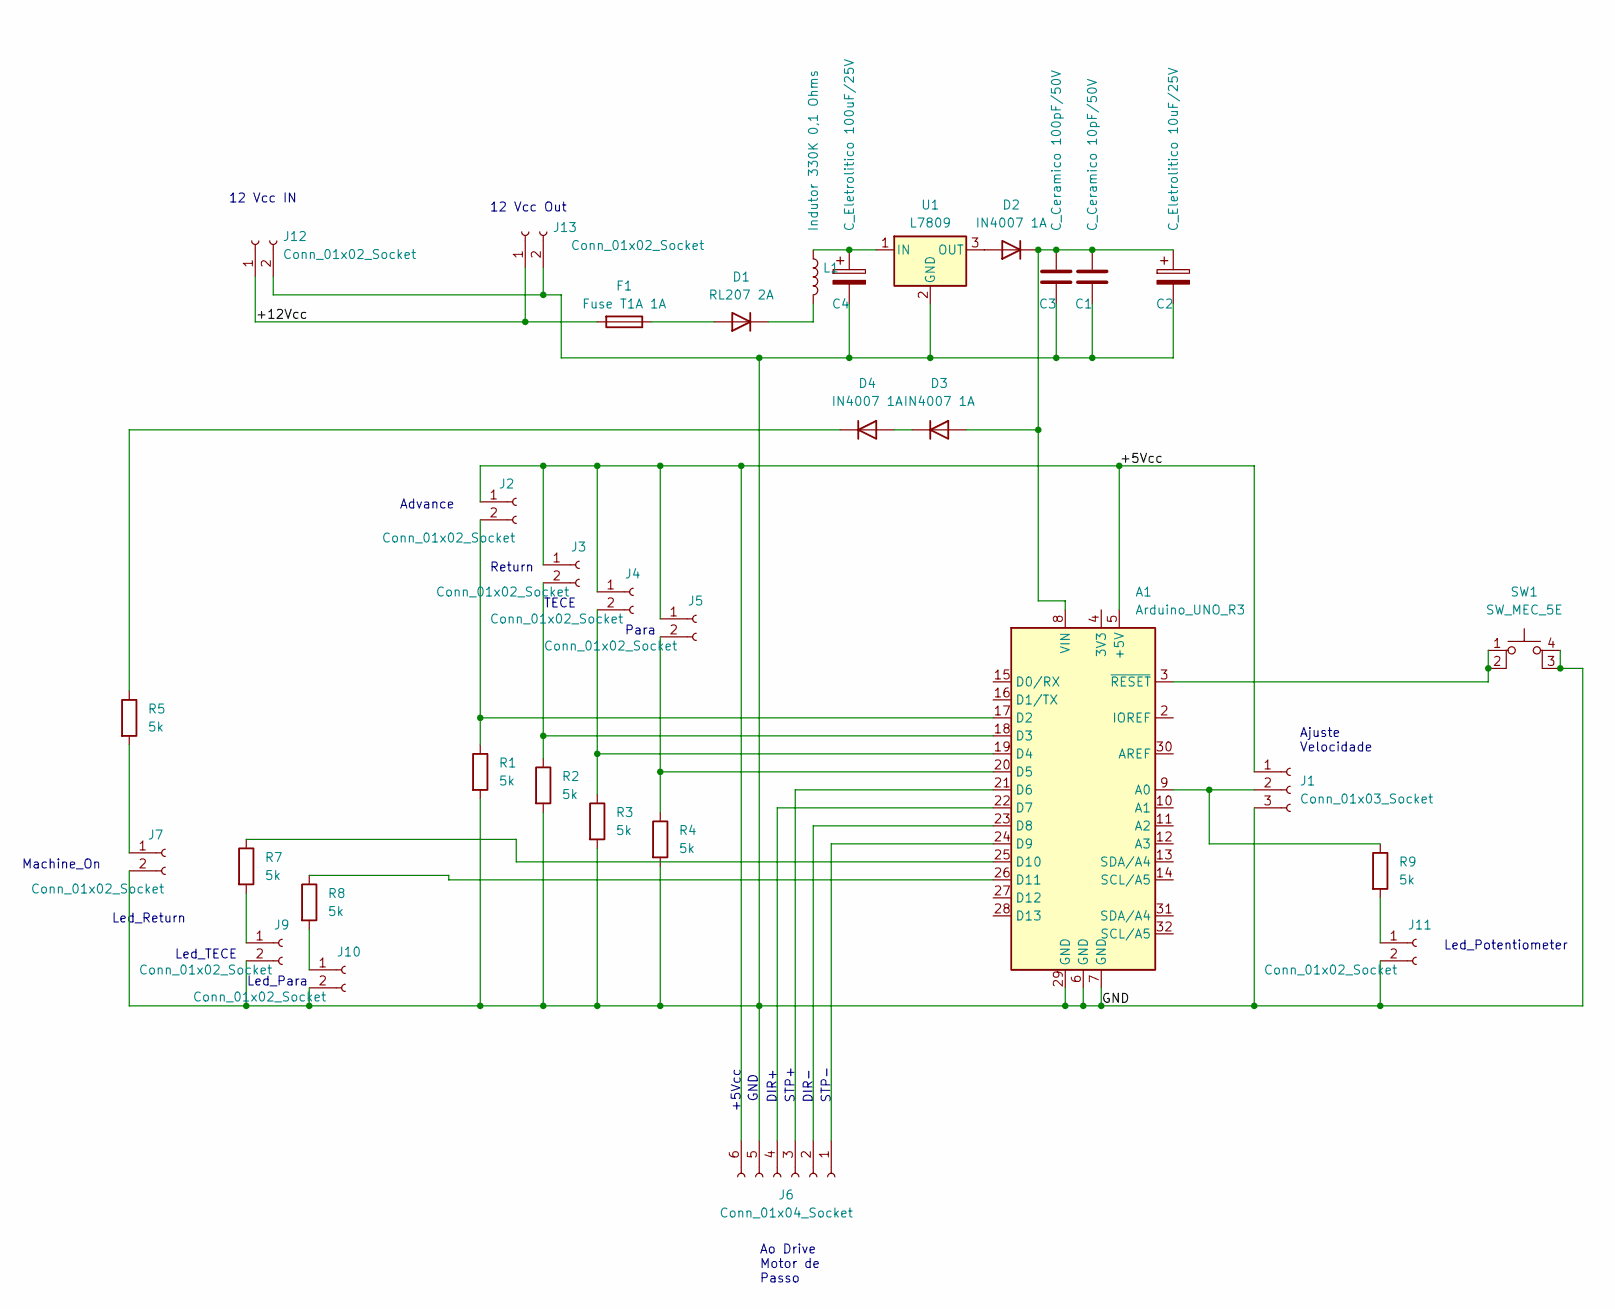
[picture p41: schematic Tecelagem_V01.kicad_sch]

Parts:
A1: Arduino_UNO_R3
C1: C_Ceramico 10pF/50V; C_Disc_D3.0mm_W1.6mm_P2.50mm
C2: C_Eletrolitico 10uF/25V; CP_Radial_D5.0mm_P2.50mm
C3: C_Ceramico 100pF/50V; C_Disc_D3.0mm_W1.6mm_P2.50mm
C4: C_Eletrolitico 100uF/25V; CP_Radial_D5.0mm_P2.50mm
D1: RL207 2A; D_DO-27_P5.08mm_Vertical_AnodeUp
D2, D3, D4: IN4007 1A; D_DO-15_P3.81mm_Vertical_AnodeUp
F1: Fuse T1A 1A; Fuse_Littelfuse_372_D8.50mm
J1: Conn_01x03_Socket; Molex_KK-254_AE-6410-03A_1x03_P2.54mm_Vertical
J2, J3, J4, J5, J7, J9, J10, J11: Conn_01x02_Socket; Molex_KK-254_AE-6410-02A_1x02_P2.54mm_Vertical
J6: Conn_01x04_Socket; Molex_KK-254_AE-6410-06A_1x06_P2.54mm_Vertical
J12, J13: Conn_01x02_Socket; Molex_KK-396_A-41791-0002_1x02_P3.96mm_Vertical
L1: Indutor 330K 0,1 Ohms; L_Radial_D7.8mm_P5.00mm_Fastron_07HCP
R1, R2, R3, R4, R5, R7, R8, R9: 5k; R_Axial_DIN0204_L3.6mm_D1.6mm_P1.90mm_Vertical
SW1: SW_MEC_5E; Tactil_6mm
U1: L7809; TO-126-3_Vertical

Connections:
/+5Vcc: A1.5 (+5V), J1.1, J2.1, J3.1, J4.1, J5.1, J6.6
/+12Vcc: F1.2, J12.1, J13.1
/GND: A1.6 (GND), A1.7 (GND), A1.29 (GND), C1.2, C2.2, C3.2, C4.2, J1.3, J6.5, J7.2, J9.2, J10.2, J11.2, J12.2, J13.2, R1.2, R2.2, R3.2, R4.2, SW1.3 (K), SW1.4 (A), U1.2 (GND)
unnamed: A1.9 (A0), J1.2, R9.1
unnamed: A1.17 (D2), J2.2, R1.1
unnamed: A1.18 (D3), J3.2, R2.1
unnamed: A1.19 (D4), J4.2, R3.1
unnamed: A1.20 (D5), J5.2, R4.1
unnamed: A1.21 (D6), J6.3
unnamed: A1.22 (D7), J6.4
unnamed: A1.23 (D8), J6.2
unnamed: A1.24 (D9), J6.1
unnamed: A1.25 (D10), R7.1
unnamed: A1.26 (D11), R8.1
unnamed: A1.8 (VIN), C1.1, C2.1, C3.1, D2.1 (K), D3.2 (A)
unnamed: A1.3 (~RESET), SW1.1, SW1.2
unnamed: D1.2 (A), F1.1
unnamed: D1.1 (K), L1.2
unnamed: D2.2 (A), U1.3 (OUT)
unnamed: D3.1 (K), D4.2 (A)
unnamed: D4.1 (K), R5.1
unnamed: J7.1, R5.2
unnamed: J9.1, R7.2
unnamed: J10.1, R8.2
unnamed: J11.1, R9.2
unnamed: C4.1, L1.1, U1.1 (IN)

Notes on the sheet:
Para
Led_Para
12 Vcc IN
TECE
Led_TECE
GND
Ajuste Velocidade
Led_Return
+5Vcc
Machine_On
Ao Drive Motor de Passo
Advance
12 Vcc Out
STP+
DIR-
Return
Led_Potentiometer
DIR+
STP-

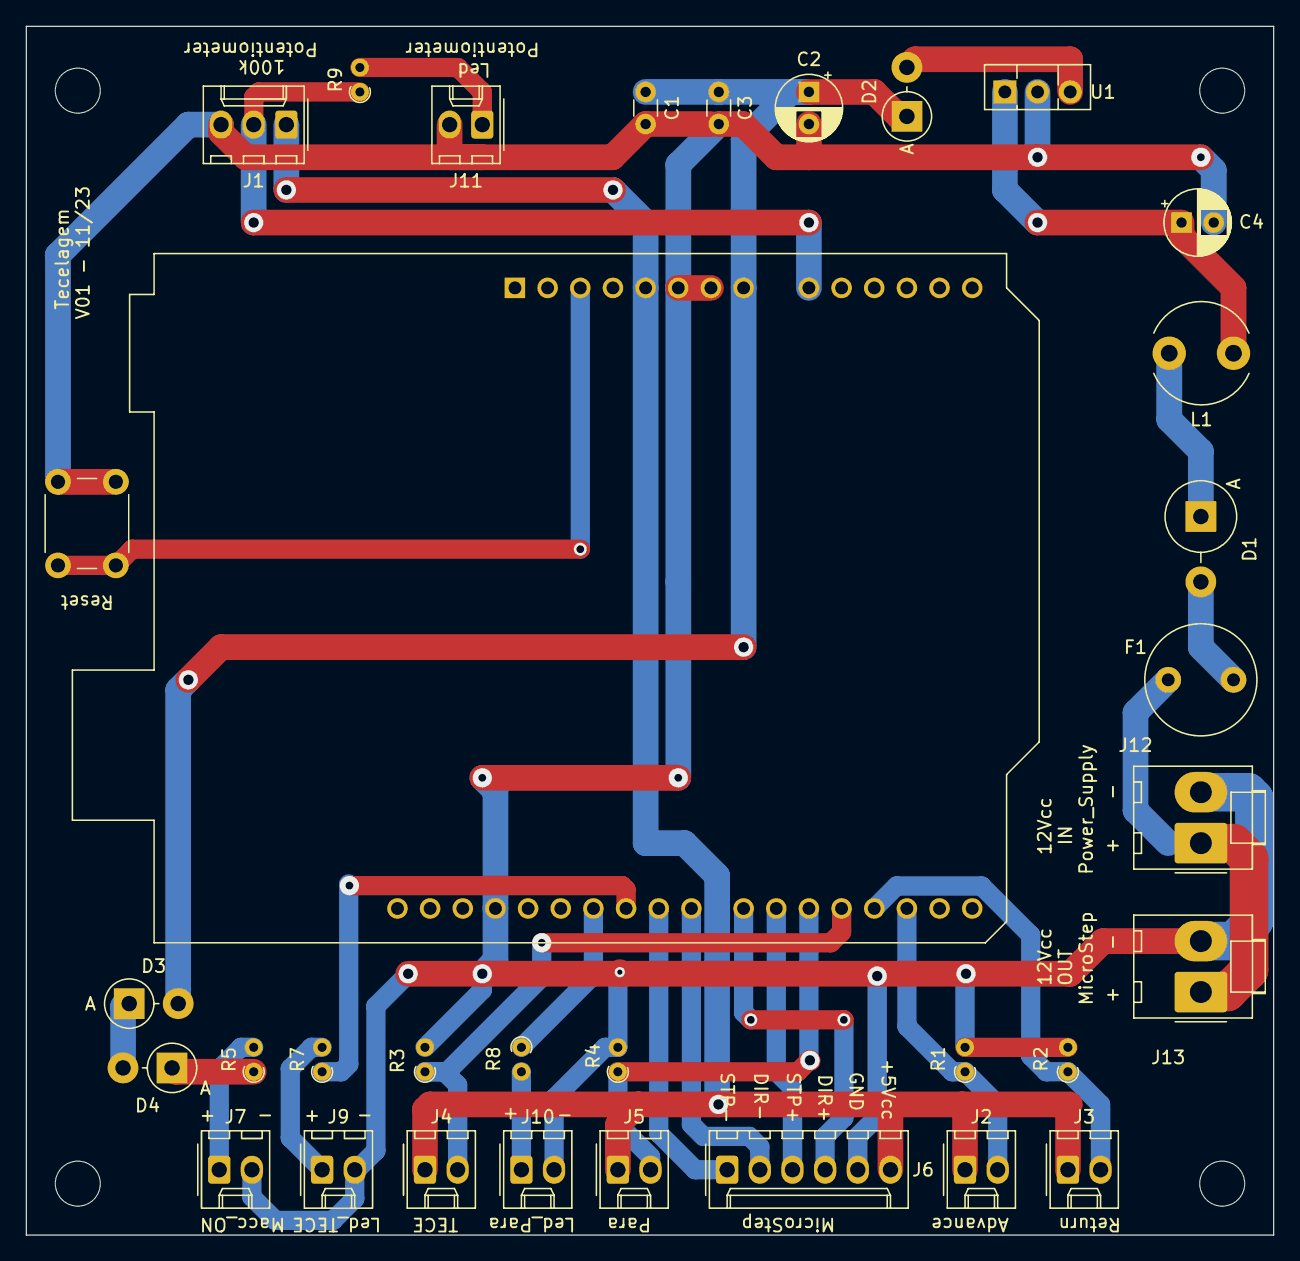
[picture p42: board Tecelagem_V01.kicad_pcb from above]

Board: 2 copper layers, 97.0 x 94.0 mm, 33 parts (0 on the bottom side), 26 nets.

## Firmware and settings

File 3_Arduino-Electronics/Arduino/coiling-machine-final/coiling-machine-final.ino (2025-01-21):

//    Macro Yarn Machine, designed by Jasmin Martinez
//    Code by Julio Augusto Martinez

// To change motor direction, change "dir" from HIGH to LOW and vice versa.

//    1 botao para tecer
//    1 botao para parar de tecer
//    1 botao para girar passo a passo para frente
//    1 botao para girar passoa a passo para trás
//    1 potenciometro para regular a velocidade (sp)
//    1 chave para ligar e desligar a tecelagem

// Versao 01 --> Versao inicial

//#include <Stepper.h>
bool TECE = 0;
bool chaveon = 0;
bool chaveoff = 0;
bool chaveEnd = 0;

int x = 0;

const int buttonAvance = 2;     // the number of the pushbutton pin
const int buttonReturn = 3;     // the number of the pushbutton pin
const int buttonLiga = 4;     // the number of the pushbutton pin
const int buttonPara = 5;     // the number of the pushbutton pin
const int stp = 9;  //connect pin 6 to step
const int dir = 8;  // connect pin 7 to direcao
const int Led_Tece = 10;  // connect pin 10 led de Tecendo
const int Led_Para = 11;  // connect pin 11 led de tecelagem parada

int sp = 0;
#define pot A0
unsigned long turnon = 0;
unsigned long turnoff = 0;



// variables will change:
int button_Avance_State = 0;         // variable for Avance the pushbutton status
int button_Return_State = 0;         // variable for Avance the pushbutton status
int button_Liga_State = 0;         // variable for Avance the pushbutton status
int button_Para_State = 0;         // variable for Avance the pushbutton status

int stepCount = 0;         // number of steps the motor has taken

int Soma = 0;

int Memoria_Avance = LOW;   // the previous Avance from the input pin
int Memoria_Return = LOW;   // the previous Avance from the input pin
int Memoria_Liga = LOW;   // the previous Avance from the input pin
int Memoria_Para = LOW;   // the previous Avance from the input pin

// the following variables are unsigned longs because the time, measured in
// milliseconds, will quickly become a bigger number than can be stored in an int.
unsigned long lastDebounceTime = 0;  // the last time the output pin was toggled
unsigned long debounceDelay = 50;    // the debounce time; increase if the output flickers

void setup() {
  // initialize the serial port:
  Serial.begin(9600);
  pinMode(buttonAvance, INPUT);
  pinMode(buttonReturn, INPUT);
  pinMode(buttonLiga, INPUT);
  pinMode(buttonPara, INPUT);
  pinMode(stp, OUTPUT);
  pinMode(dir, OUTPUT);  
  pinMode(Led_Tece, OUTPUT);  
  pinMode(Led_Para, OUTPUT);
 
  digitalWrite(dir, HIGH);
  //digitalWrite(dir2, LOW);
  delay(100);
}

void loop() {
  // read the state of the switch into a local variable:
  int Avance = digitalRead(buttonAvance);
  int Return = digitalRead(buttonReturn);
  int Liga = digitalRead(buttonLiga);
//  int Para = digitalRead(buttonPara);
  //Serial.println(Return);

  // If the switch changed, due to noise or pressing:
  if ((Avance != Memoria_Avance) or (Return != Memoria_Return) or (Liga != Memoria_Liga)/* or (Para != Memoria_Para)*/){
    // reset the debouncing timer
    lastDebounceTime = micros();
  }

  if ((micros() - lastDebounceTime) > debounceDelay) {
    // if the button state has changed:
    if (Avance != button_Avance_State) 
     {
      button_Avance_State = Avance;x=0;
      if (button_Avance_State == HIGH) 
         {
          digitalWrite(dir, LOW);
          while(x<=20)
          {
           digitalWrite(stp, HIGH);
           delay(1);
           digitalWrite(stp, LOW);
           delay(1);
           x++;
           }
          }
       }  
      if (Return != button_Return_State)
      {
        button_Return_State = Return;
        if (button_Return_State == HIGH)
         {
          digitalWrite(dir, HIGH);x=0;
          while(x<=20)
           {
            digitalWrite(stp, HIGH);
            delay(1);
            digitalWrite(stp, LOW);
            delay(1);
            x++;
           }
         }
      } 

      if (Liga != button_Liga_State)
       {
        button_Liga_State = Liga;
        if (button_Liga_State == HIGH) TECE = 1;
        digitalWrite(dir, HIGH); 
       }
    }

  // Salva o avance. Proxima vez atraves do loop sera Memoria_Avances:
  Memoria_Avance = Avance;  
  Memoria_Return = Return;
  Memoria_Liga = Liga;

  if (TECE == 1) {
    digitalWrite(Led_Tece, HIGH);
    digitalWrite(Led_Para, LOW);
  }
  else
  {
    digitalWrite(Led_Tece, LOW);
    digitalWrite(Led_Para, HIGH);
  }
  
  while(TECE == 1)
  {
    sp = map((analogRead(pot)), 0,1023, 1000, 0); // Tratamento da velocidade do motor
    digitalWrite(stp, HIGH);
    delayMicroseconds(sp + 275);
    digitalWrite(stp, LOW);
    delayMicroseconds(sp + 275);      
    //Serial.println();
    //Serial.print("sp");
    //Serial.println(sp);

  // Tratamento da informacao do botao de parar
  int Para = digitalRead(buttonPara);
  // If the switch changed, due to noise or pressing:
  if ((Para != Memoria_Para))
   {
    // reset the debouncing timer
    lastDebounceTime = micros();
   }

  if ((micros() - lastDebounceTime) > debounceDelay)
   { 
    if (Para != button_Para_State)
     {
      button_Para_State = Para;
      if (button_Para_State == HIGH) 
       {
        TECE = 0;
        digitalWrite(stp, LOW);
       }
     }
   }
    Memoria_Para = Para; 
  }
}

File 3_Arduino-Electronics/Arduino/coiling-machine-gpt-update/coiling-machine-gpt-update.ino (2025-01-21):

//    Macro Yarn Machine, designed by Jasmin Martinez, 2024
//    Paludi Coiling Machine, designed by Jasmin Martinez, 2025
//    Code by Julio Augusto Martinez, 2024

// To change motor direction, update the "motorDirection" variable to HIGH or LOW.
// Use HIGH for one direction and LOW for the reverse direction.

#include <Arduino.h>

// Variables to control the motor
const int motorStepPin = 9;  // Connect to the STEP pin
const int motorDirPin = 8;   // Connect to the DIR pin

// Define the default motor direction
// Change this value to set the initial direction: HIGH or LOW
// For the Coiling Machine, HIGH is counterclockwise.

int motorDirection = HIGH; 

bool TECE = 0;
int x = 0;

// Pin assignments for buttons
const int buttonAvance = 2;     
const int buttonReturn = 3;    
const int buttonLiga = 4;      
const int buttonPara = 5;      
const int potPin = A0;         

// LED pins
const int Led_Tece = 10;       
const int Led_Para = 11;       

// Variables to handle button states
bool chaveon = 0, chaveoff = 0, chaveEnd = 0;
int button_Avance_State = 0, button_Return_State = 0, button_Liga_State = 0, button_Para_State = 0;
int Memoria_Avance = LOW, Memoria_Return = LOW, Memoria_Liga = LOW, Memoria_Para = LOW;

// Debounce settings
unsigned long lastDebounceTime = 0;  
const unsigned long debounceDelay = 50; 

void setup() {
  Serial.begin(9600);

  // Configure pins
  pinMode(buttonAvance, INPUT);
  pinMode(buttonReturn, INPUT);
  pinMode(buttonLiga, INPUT);
  pinMode(buttonPara, INPUT);
  pinMode(motorStepPin, OUTPUT);
  pinMode(motorDirPin, OUTPUT);
  pinMode(Led_Tece, OUTPUT);
  pinMode(Led_Para, OUTPUT);

  // Set initial motor direction
  digitalWrite(motorDirPin, motorDirection); 
  delay(100);
}

void loop() {
  // Read button states
  int Avance = digitalRead(buttonAvance);
  int Return = digitalRead(buttonReturn);
  int Liga = digitalRead(buttonLiga);

  // Debounce buttons
  if ((Avance != Memoria_Avance) || (Return != Memoria_Return) || (Liga != Memoria_Liga)) {
    lastDebounceTime = micros();
  }

  if ((micros() - lastDebounceTime) > debounceDelay) {
    if (Avance != button_Avance_State) {
      button_Avance_State = Avance;
      if (button_Avance_State == HIGH) {
        motorDirection = LOW;  // Set direction for avance
        digitalWrite(motorDirPin, motorDirection);
        stepMotor(20);
      }
    }

    if (Return != button_Return_State) {
      button_Return_State = Return;
      if (button_Return_State == HIGH) {
        motorDirection = HIGH;  // Set direction for return
        digitalWrite(motorDirPin, motorDirection);
        stepMotor(20);
      }
    }

    if (Liga != button_Liga_State) {
      button_Liga_State = Liga;
      if (button_Liga_State == HIGH) TECE = 1;
    }
  }

  // Save button states
  Memoria_Avance = Avance;
  Memoria_Return = Return;
  Memoria_Liga = Liga;

  // Handle motor operation
  manageMotor();
}

void stepMotor(int steps) {
  for (int i = 0; i < steps; i++) {
    digitalWrite(motorStepPin, HIGH);
    delay(1);
    digitalWrite(motorStepPin, LOW);
    delay(1);
  }
}

void manageMotor() {
  if (TECE == 1) {
    digitalWrite(Led_Tece, HIGH);
    digitalWrite(Led_Para, LOW);

    while (TECE == 1) {
      int sp = map(analogRead(potPin), 0, 1023, 1000, 0);
      digitalWrite(motorStepPin, HIGH);
      delayMicroseconds(sp + 275);
      digitalWrite(motorStepPin, LOW);
      delayMicroseconds(sp + 275);

      // Handle stop button
      int Para = digitalRead(buttonPara);
      if ((Para != Memoria_Para) && (micros() - lastDebounceTime > debounceDelay)) {
        button_Para_State = Para;
        if (button_Para_State == HIGH) {
          TECE = 0;
          digitalWrite(motorStepPin, LOW);
        }
      }
      Memoria_Para = Para;
    }
  } else {
    digitalWrite(Led_Tece, LOW);
    digitalWrite(Led_Para, HIGH);
  }
}
